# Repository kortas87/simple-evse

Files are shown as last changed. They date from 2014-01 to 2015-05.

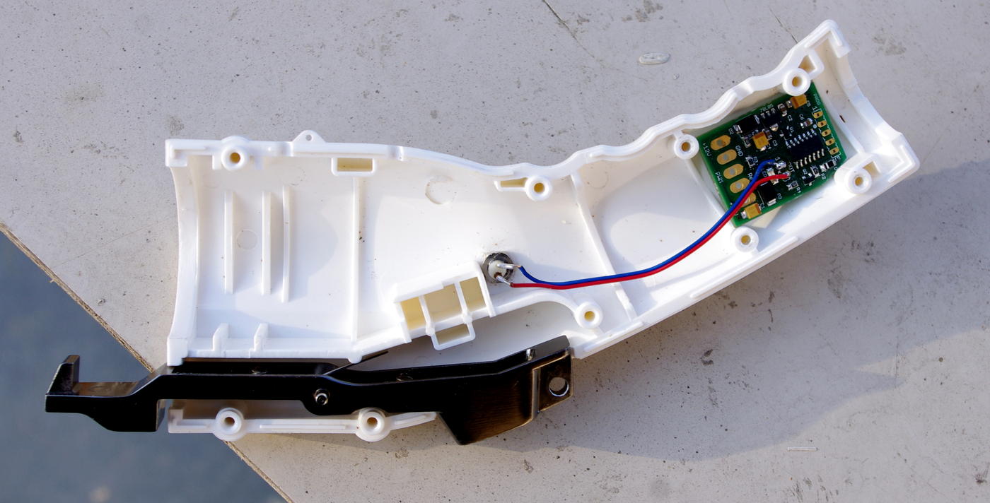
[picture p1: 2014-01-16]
images/j1772_LED_installed.jpg

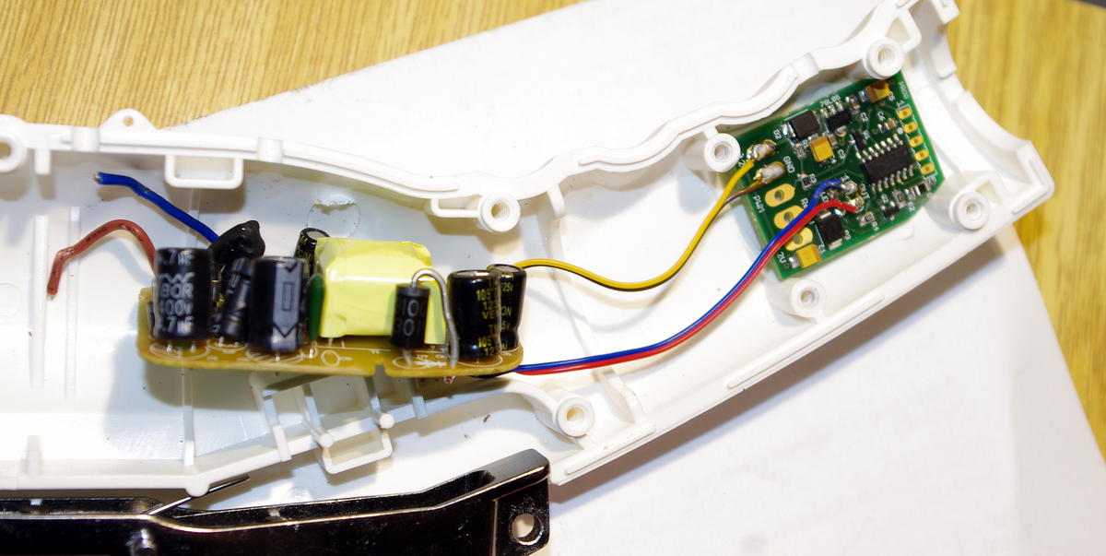
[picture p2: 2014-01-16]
images/j1772_DC-12V_installed.jpg

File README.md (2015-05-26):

# NEWS #

**24.12.2014**

---

At the moment we are testing new sealed AC/DC converters which should replace the original black 12V 500mA power adapters. The greatest advantage is that these power supply units are small enough to fit in the connector J1772 easily (no need for pushing or changing anything) and they are more or less water resistant (please do not forget that in the connector there are usually other things as well which may cause short if too much of water gets in - e.g. relay contacts)

## Project introduction ##

We have developed a board based on PIC microcontroller which is able to generate 1kHz PWM signal, detect the vehicle and control the relay. It is also possible to adjust PWM width for current regulation. The board is small enough to be installed directly into J1772 Yazaki connector.

The kit can be obtained from [EV Power](http://www.ev-power.eu/index.php?cl=search&searchparam=EVSE) (Czech Republic).

  * [How to make your own J1772 connector with EVSE](SimpleEvseJ1772guide.md)
  * [J1772 button connection scheme](J1772buttonConnectionSchematic.md)
  * [Setting different charging current limit (6 - 20A)](HowToSetDifferentCurrentLimit.md)





# EVSE Kit includes #

1. Mounted PCB including microcontroller with latest [firmware](http://code.google.com/p/simple-evse/source/checkout)



2. 12V DC power supply



3. AC relay 230V 20A



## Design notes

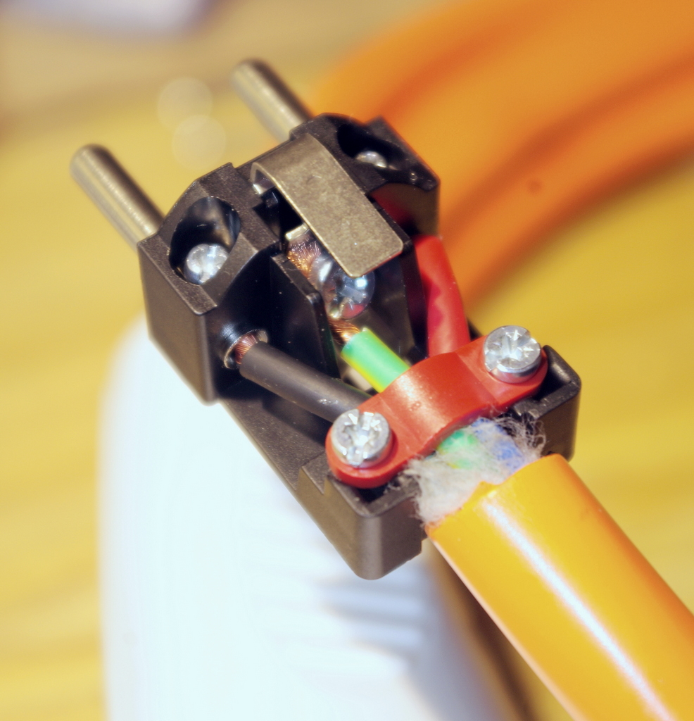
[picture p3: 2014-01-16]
images/schuko.jpg

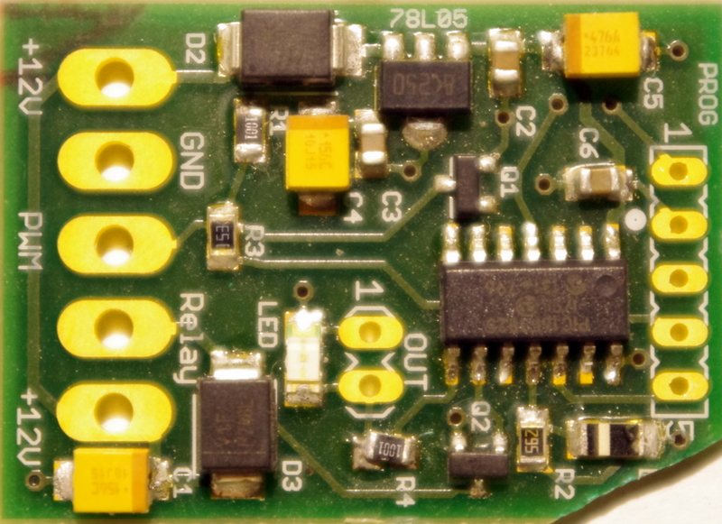
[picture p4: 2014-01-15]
images/board_small.jpg

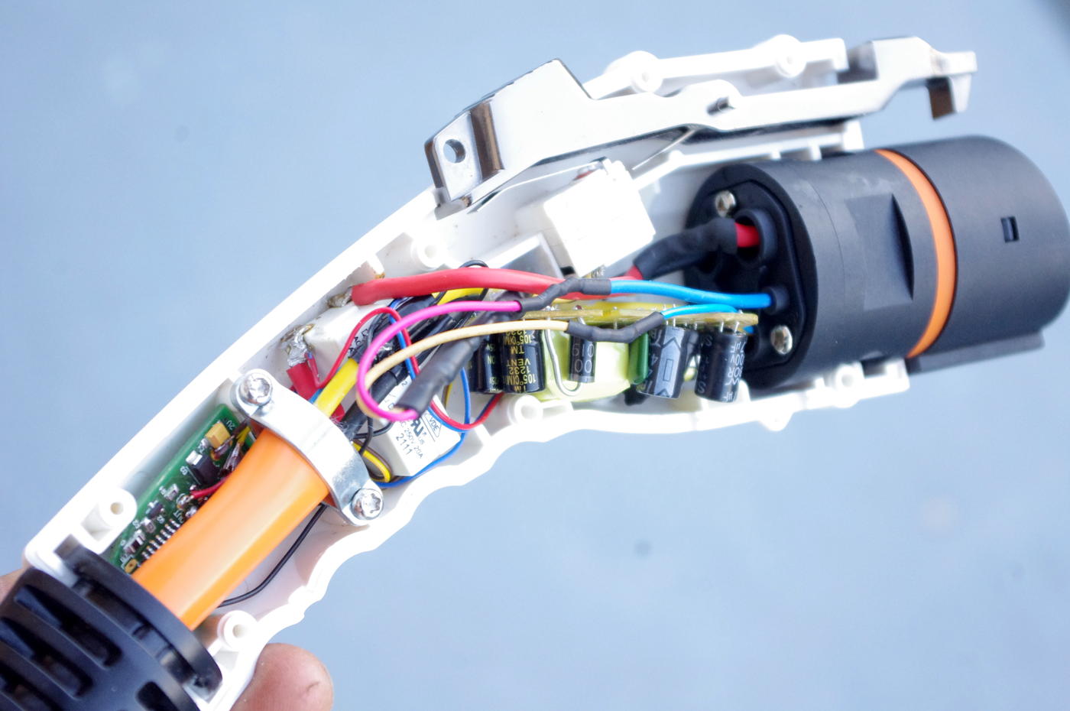
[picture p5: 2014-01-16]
images/j1772_final_before_covering.jpg

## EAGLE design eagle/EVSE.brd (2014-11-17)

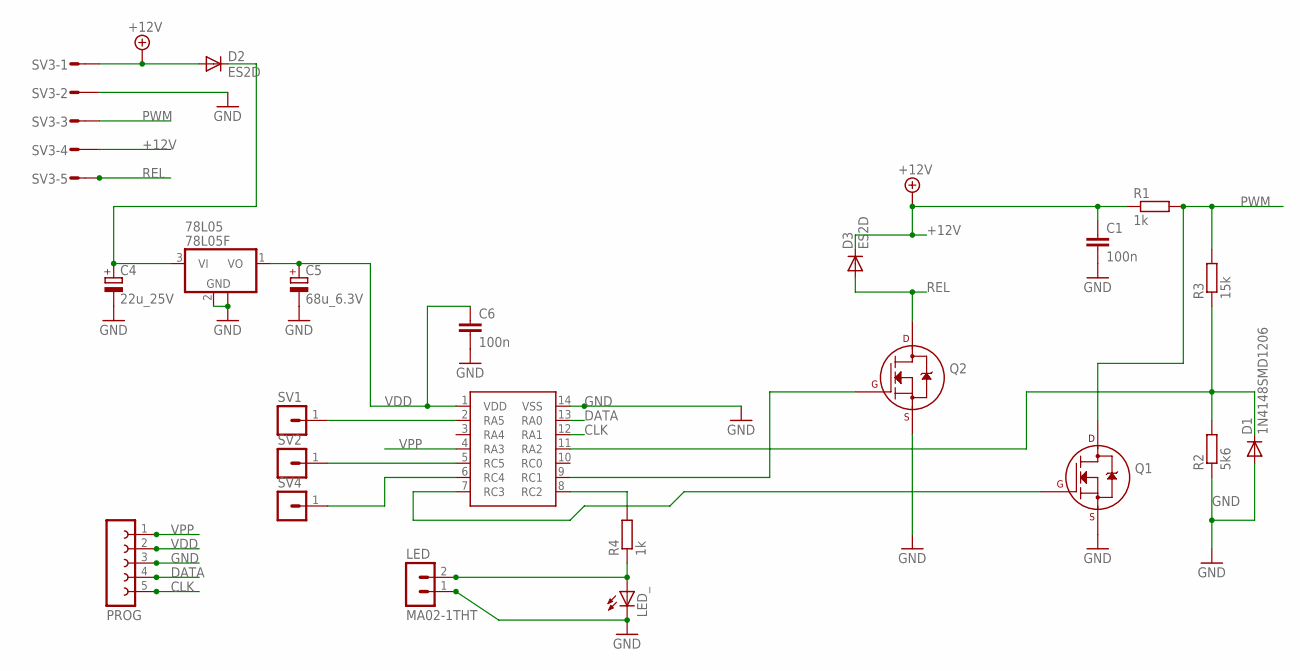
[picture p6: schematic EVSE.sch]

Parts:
78L05: 78L05F; SOT89
C1, C6: 100n; C0805
C4: 22u_25V; B/3528-21W
C5: 68u_6.3V; B/3528-21W
D1: 1N4148SMD1206; D1206
D2, D3: ES2D; SMB
LED: MA02-1THT; MA02-1
LED_: LEDSMT1206; 1206
PIC16F1825: PIC16F1825SOIC; SO-14
PROG: FE05-1
Q1, Q2: 2N7002_SOT23; SOT-23
R1, R4: 1k; R0805
R2: 5k6; R0805
R3: 15k; R0805
SV1, SV2, SV4: PIN-HEADER1
SV3: MT6-5

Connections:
+12V: C1.1, D2.A, D3.C, R1.1, SV3.1, SV3.4
CLK: PIC16F1825.12 (RA1), PROG.5
DATA: PIC16F1825.13 (RA0), PROG.4
GND: 78L05.2 (GND), 78L05.2@1 (GND), C1.2, C4.-, C5.-, C6.2, D1.A, LED.1, LED_.C, PIC16F1825.14 (VSS), PROG.3, Q1.2 (S), Q2.2 (S), R2.1, SV3.2
unnamed: 78L05.3 (VI), C4.+, D2.C
unnamed: D1.C, PIC16F1825.11 (RA2), R2.2, R3.1
unnamed: PIC16F1825.7 (RC3), Q1.1 (G)
unnamed: PIC16F1825.2 (RA5), SV1.1
unnamed: PIC16F1825.9 (RC1), Q2.1 (G)
unnamed: PIC16F1825.5 (RC5), SV2.1
unnamed: PIC16F1825.6 (RC4), SV4.1
unnamed: PIC16F1825.8 (RC2), R4.2
unnamed: LED.2, LED_.A, R4.1
PWM: Q1.3 (D), R1.2, R3.2, SV3.3
REL: D3.A, Q2.3 (D), SV3.5
VDD: 78L05.1 (VO), C5.+, C6.1, PIC16F1825.1 (VDD), PROG.2
VPP: PIC16F1825.4 (RA3), PROG.1

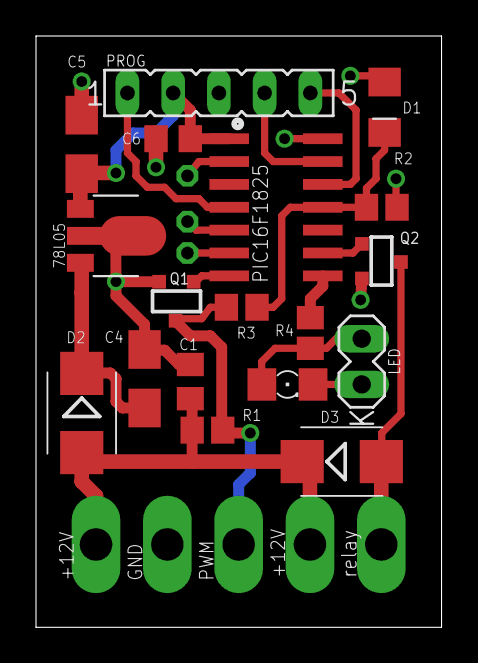
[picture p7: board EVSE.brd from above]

Board: 2 copper layers, 22.5 x 32.9 mm, 22 parts (0 on the bottom side), 17 nets.

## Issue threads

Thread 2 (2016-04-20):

delay before switching to 10A

InnovativeIdeas, 2016-04-20:
The current code has two issues as I see it

1. the PWM signal should only start on car detection  ( i.e. from open to 2740 ohms in circuit)
whereas now immediately generates the pwm

2. the code delays on power before switching from the default 16A to 10A or 6A.  the default should be changed to start at the lowest power or else detect pin 5 before generating  the ppm

there is a danger that the car could draw 16A first before switching to lower command currents and this is incorrect

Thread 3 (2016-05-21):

schuko.jpg shows bad installation

CosmicDuck, 2016-05-21:
Hello,

your photo shows a very bad installation of a cable in the schuko, a picture who never should do this in this way.
1. Never use direct the power wires for the cord grip. The cables insulation coat must be jammed by the cord grip.
2. The PE must be little bit longer than all other wires. Long enough so if the cord grip will not work the
PE is the latest cable which should leave the clamps (which hopefully never do).
Here is a good description which I found (in germany) http://www.perlenwiki.de/index.php/Schukostecker
If the cable coat is to thick use a bigger schuko plug ;-)

kirk-loeten, 2019-07-30:
This picture is very bad. Please delete the picture.

kirk-loeten, 2019-07-31:
@kortas87 Please use this Picture, it is free to use.
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

kirk-loeten, 2019-07-31:
@CosmicDuck Die Anleitung ist aber auch nicht ganz richtig. Da der PE schon etwas vor den anderen Kontakten liegt, kann man die Adern gleich lang machen.

CosmicDuck, 2022-03-28:
Hallo,

das ist im Prinzip schon richtig und bei dem von mir vorgestelltem Bild so möglich. Aber das macht das Original Bild nicht besser da dort der auch noch PE gekürzt wurde.

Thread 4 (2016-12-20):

Relay Output Always ON

jhauwel, 2016-12-20:
Hello,

I have a problem with a simple-evse card.
The Relay Output Always ON.
The PWM signal has no negative component.
Which component creates negative power?

Thank you in advance.
Johan

tofelec, 2017-12-29:
hello,same issue ere...someone kan help?

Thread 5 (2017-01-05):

firmwhare

dmejer1, 2017-01-05:
Hello.
Can you help me please? Where i can get a firmwhare for you simple evse in connector,

stemp1975, 2017-06-25:
Good afternoon, Kortas87!
I was interested in your project.
Could you put the HEX file for the firmware PIC16F1824.
Thanks in advance.
Alexander

dmejer1, 2017-06-25:
Я когда-то пробовал туда писать но так никто и не ответил

воскресенье, 25 июня 2017 г. пользователь stemp1975 написал:

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

dmejer1, 2017-06-26:
Александр здравствуйте
Ну как у вас есть какие то новости?

2017-06-25 23:07 GMT+03:00 Dmitriy Meyer <dmejer2@gmail.com>:

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

stemp1975, 2017-06-27:
Добрый вечер, Дмитрий!Прошивку на языке С (предположительно) я вытащил из одной папки, по той ссылке.
Сегодня написал одному разработчику поделок на Ардуино, но он, к сожалению, не сможет с этим помочь.
Вот программа.
Напишу еще на одном форуме, может кто ответит.

26 червня 2017, 20:46:13, від "dmejer1" <notifications@github.com>:

Александр здравствуйте
Ну как у вас есть какие то новости?

2017-06-25 23:07 GMT+03:00 Dmitriy Meyer <dmejer2@gmail.com>:

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

—
You are receiving this because you commented.
Reply to this email directly, view it on GitHub, or mute the thread.

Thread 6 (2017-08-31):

Is this project still alive?

RomeuCarvalhoPT, 2017-08-31:
Hi guys.
Is this project still alive?
I was planing to buy one of this boards (simple evse wallbox) to build my own charger.
There are any new developments? any support?
I don't see anithing related to the wallbox version here.

Thank you

goctav2000, 2019-06-14:
Hi Kortas .
I already bought EVSE-KIT-W16 (https://www.ev-power.eu/Electric-Cars/EVSE-Kit-v1-1-for-EV-charging-station-cable-2x16A-relay-kit-only.html)
Is possible to controlling the EVSE-KIT-W16 by Fronius Data manager 2 ---RS485 communication ? to using  for charging EV by  PV power ?
my gabriel.tanasescu03@gmail.com

[SE_WP_E-Mobility_Solutions_EN.pdf](https://github.com/kortas87/simple-evse/files/3291792/SE_WP_E-Mobility_Solutions_EN.pdf)

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

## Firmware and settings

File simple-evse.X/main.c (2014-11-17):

/*
 * File:   main.c
 * Author: Petr Kortanek, i4wifi a.s.
 *
 * Created on 23rd November 2013
 *
 * 2014-01-11 - RA3 (MCLR, prog 1) input for button
 * 2014-04-09 - RA0 (ICSPDAT, prog 4) potentiometer input
 * 2014-08-11 - fixed PWM duty (+10bit), RA1 (ICSPCLK, prog 5) input switch 6A / 10A
 */

#include <stdio.h>
#include <stdlib.h>
#include <xc.h>

#define _XTAL_FREQ 4000000
#define Button_pressed PORTAbits.RA3

#pragma config LVP = OFF, MCLRE = OFF, BOREN = OFF, PLLEN = OFF, FOSC = INTOSC, WDTE = OFF, CP = OFF, PWRTE = OFF

char latcha = 0;
char latchc = 0;
char pilot_value = 255;
char pot_value = 255;
char pot_value2 = 255;
char adchannel = 2;
char measure_nth = 0;
char button_pressed_counter = 0;
char amps = 16;
char amps_to_set = 16;
char setbypot = 0;
short duty = 500; //50%

//attached to RC1
void relayon() {
  latchc = latchc | 0b00000011;//RC1+backup RC0
  PORTC = latchc;
}
void relayoff() {
  latchc = latchc & 0b11111100;//RC1+backup RC0
  PORTC = latchc;
}

//attached to RC2
void ledon() {
  latchc = latchc | 0b00000100;
  PORTC = latchc;
}
void ledoff() {
  latchc = latchc & 0b11111011;
  PORTC = latchc;
}

void button_flashing() {
  for (int i=0; i<20; i++) {
    ledon();
    __delay_ms(30);
    ledoff();
    __delay_ms(30);
  }
}

void setAmps() {
  setbypot = 0;

  //we get current limit from the pot
  if (pot_value <= 222) { //<4.4V, amps 6-80
    amps = 6 + (222-pot_value)/3;
    setbypot = 1;
  }
  //we get current limit from the "pot2" (set 6A / 10A)
  if (pot_value2 <= 222) { //<4.4V,
    amps = 10;
    if (pot_value2 <= 25) { //short => amps 6 ~ >3kOhm
      amps = 6;
    }
    setbypot = 1;
  }
  if (setbypot == 0) {
    amps = amps_to_set;
  }
  //minimum
  if (amps < 5)
    amps = 5;
  //maximum
  if (amps > 80)
    amps = 80;
  
  //compute PWM duty
  if (amps < 51)
    duty = 1000 - (100 * amps) / 6;
  else
    duty = 1000 - (4*amps+640);

  //set PWM output 10bit
  CCPR1L = duty >> 2;
  duty &= 0b00000011;
  duty <<= 4;
  CCP1CON = duty + 12; //1100

}

void main() {

    OSCCON = 0b01101010; // 4MHz

    TRISA = 0b11111111; //pilot detect RA2, button detect RA3, pot RA0, pot2 RA1
    TRISC = 0b11110000; //relay RC1 (+backup RC0), LED RC2, pilot RC3
    latcha = 0;
    latchc = 0;
    PORTA = latcha;
    PORTC = latchc;

    ADCON1 = 0b01100000; // f/64 4MHz, 16 us
    ADON = 1; //channel: RA2=PWM detect, RA0=pot value, RA1=pot2 value
    ADCON0bits.CHS = 2;

    //pilot PWM RC3
    PSTR1CONbits.STR1C = 1;
    APFCON1bits.P1CSEL = 0; //P1C function is on RC3
    
    PR2 = 249 ;//period value
    CCP1CON = 0b00001100; //PWM mode

    OPTION_REG = 0b00000001; //pullups and TMR0
    WPUAbits.WPUA3 = 1; //button pressed detect - MCLR
    WPUAbits.WPUA1 = 1;  //6A / 10A input RA1

    //T2CON timer ON + prescaler 4
    T2CON = 0b00000101 ;

    //INTCON = 0b11100000;
    GIE = 1;
    PEIE = 1;
    
    ADIE = 1;
    TMR2IE = 1;
    
    setAmps();

    while(1) {

        //MODE set current
        if(Button_pressed == 0) {
          button_pressed_counter++;
          //setting mode entered - rapid led flashing
          if (button_pressed_counter == 5) {
            button_flashing();
            amps_to_set = 0;
          }
          if (button_pressed_counter >= 5) {
            amps_to_set++;
            setAmps();
            ledoff();
            __delay_ms(300);
            ledon();
            __delay_ms(300);
          } else {
            __delay_ms(800);
          }

        //MODE normal operation
        } else {
          if(button_pressed_counter>=5) {
            //current setting mode exit confirmation
            button_flashing();
          }
          button_pressed_counter = 0;

          //car connected (pilot pulled down <8V)
          if(pilot_value < 111) {
            relayon();
            ledon();
            __delay_ms(800);

          } else {
            ledon();
            __delay_ms(30);
            relayoff();
          }
          ledoff();
          __delay_ms(300);
        }
    }
}

void interrupt isr() {

  //channel: RA2=PWM detect or RA0=pot value
  if (ADIF) {
    if (adchannel == 0) {
      pot_value = ADRESH;
      setAmps();
      adchannel = 1;
    } else if (adchannel == 1) {
      pot_value2 = ADRESH;
      setAmps();
      adchannel = 2;
    } else   {
      pilot_value = ADRESH;
      adchannel = 0;
    }
    ADCON0bits.CHS = adchannel;
    ADIF = 0;
  }

  if (TMR2IF) {
    TMR2IF = 0;
    //voltage must be measured when voltage is "up"
    measure_nth++;
    if (measure_nth>98) {
      __delay_us(950);
      GO_nDONE = 1;
      measure_nth = 0;
    }
  }
}

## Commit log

2014-01-16 Directories update, added images, eagle scheme and board.
    [EVSE.brd, EVSE.sch]
2014-11-12 Changed sourcecode (current settings PWM fix, another ways of setting current)
    [main.c]
2014-11-17 Updated board layout - cosmetic changes.
    [EVSE.brd, EVSE.sch]
